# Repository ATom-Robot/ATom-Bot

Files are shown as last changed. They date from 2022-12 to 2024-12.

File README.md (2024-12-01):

# ATom-Bot 机器人
*喜欢这个项目吗？请考虑给 Star ⭐️ 以帮助改进！*

> A small desktop robot	—小型桌面交互机器人
>
> 本项目是一个桌面级小机器人，外观设计的灵感来源是Anki公司的Cozmo机器人，具备3个自由度（手臂2个、头部一个），使用自己修改的特制舵机支持关节角度回传。通过ESP32的语音唤醒+识别可以实现一些人机交互。
>
> 本项目提供了配套的全套开发资料和对应SDK以供二次开发，SDK使用说明见后文。

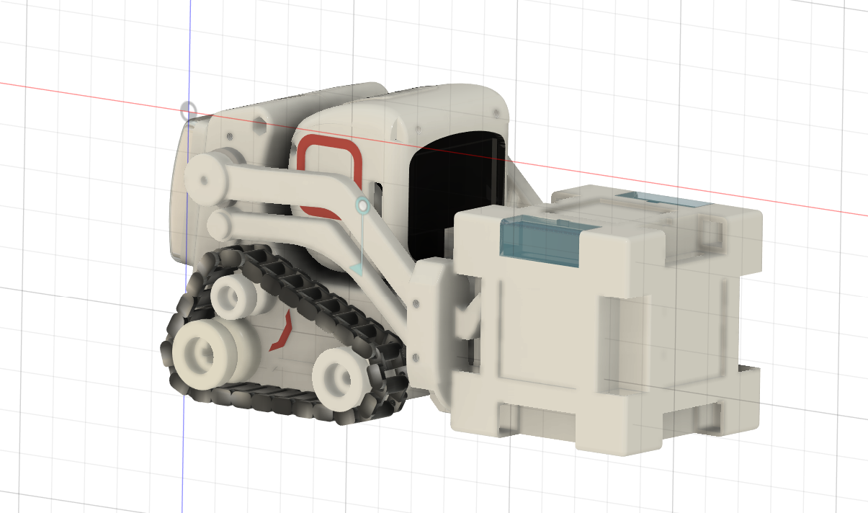
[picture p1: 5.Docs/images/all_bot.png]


机器人主要由头部+底盘两个部分组成

* 头部使用 ESP32-S3 主控担任“大脑”进行UI交互、网络通讯、轻量化AI处理；

* 底盘采用 STM32F103 主控担任“小脑”进行运动控制；

## ATom-Bot-Head 物料说明

[物料说明](https://docs.qq.com/doc/DY0lzSENnbE1SdGRn)

## ATom-Bot-Head 说明

[头部固件使用指南](https://docs.qq.com/doc/DY05KSXNtQ2pnWlF3)

## ATom-Bot-Chassis 说明

[底盘固件使用指南](https://docs.qq.com/doc/DY0NOTWp4Wk1rdlRy)

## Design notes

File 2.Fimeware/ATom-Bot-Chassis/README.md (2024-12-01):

## ATom-Bot-Chassis 说明

[底盘固件使用指南](https://docs.qq.com/doc/DY0NOTWp4Wk1rdlRy)

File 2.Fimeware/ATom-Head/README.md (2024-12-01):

# ATom-Bot-Head Fimeware

[头部固件使用指南](https://docs.qq.com/doc/DY05KSXNtQ2pnWlF3)

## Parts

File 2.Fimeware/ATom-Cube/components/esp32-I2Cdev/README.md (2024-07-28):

# I2Cdev lib for ESP32 (for MPU6050, BMP280)
I2Cdev bus implementation based on JROWBERG implementation. Modified to be more inititalized as an object, improved code consistency, some functional and structural fixes. You can find the original code here: https://github.com/jrowberg/i2cdevlib/

It is prepared to be runned as component with dependency on I2Cdev lib (https://github.com/PiotrTopa/esp32-I2Cdev). It is compatibile with PlatformIO esp-idf framework.

# Add components to your project
You need to add this repository along with I2Cdev to your project as ESP-IDF component.
```bash
cd ~/myProjects/myProject
cd components
git clone https://github.com/PiotrTopa/esp32-I2Cdev I2Cdev
```

# Example
Please see code examples at BMP280 / MPU6050 components. You can find them here:
- https://github.com/PiotrTopa/esp32-BMP280
- https://github.com/PiotrTopa/esp32-MPU6050

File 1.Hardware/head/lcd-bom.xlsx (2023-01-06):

No. | Quantity | Comment | Designator | Footprint | Value | Manufacturer Part | Manufacturer | Supplier Part | Supplier
1 | 1 | FPC-SMD_0.5-12P(翻盖下接) | CN1 | FPC-SMD_0.5S-CX-12PWB |  | FPC-SMD_0.5-12P(翻盖下接) |  | C9900007755 | LCSC
2 | 1 |  | U3 | 焊接式_TFT_1.14_135X240_13PIN
3 | 3 |  | U5,U11,U12 | 铜柱M2

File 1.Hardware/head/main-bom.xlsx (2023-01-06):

No. | Quantity | Comment | Designator | Footprint | Value | Manufacturer Part | Manufacturer | Supplier Part | Supplier
1 | 2 | TSA343G00D-250J2 | BOOT,RST | SW-SMD_L4.0-W2.9-P4.15-EH |  | TSA343G00D-250J2 | BRIGHT(博瑞泰) | C354947 | LCSC
2 | 9 | 0.1uF | C1,C4,C5,C9,C11,C14,C15,C25,C29 | C0402 | 0.1uF | 0402BB104K160NGT | Knowles(楼氏) | C2173076 | LCSC
3 | 5 | 10uF | C2,C3,C6,C24,C27 | C0402 | 10uF | CL05B104KO5NNNC | SAMSUNG(三星) | C1525 | LCSC
4 | 1 | 100nF | C7 | C0402 | 100nF | C0402X104K025T | IHHEC(禾伸堂) | C559125 | LCSC
5 | 2 | 100nF | C8,C10 | C0402 | 100nF | CL05B104KO5NNNC | SAMSUNG(三星) | C1525 | LCSC
6 | 1 | 10uF | C12 | C0402 | 10uF | C0402X104K025T | IHHEC(禾伸堂) | C559125 | LCSC
7 | 1 | 10nF | C13 | C0402 | 10nF | C0402X104K025T | IHHEC(禾伸堂) | C559125 | LCSC
8 | 1 | 10uF | C28 | C0402 | 10uF | CL05A106MQ5NUNC | SAMSUNG(三星) | C15525 | LCSC
9 | 1 | 100nF | C30 | C0402 | 100nF
10 | 1 | 10uf | C31 | C0402 | 10uf
11 | 1 | FPC-SMD_0.5-12P(翻盖下接) | CN1 | FPC-SMD_0.5S-CX-12PWB |  | FPC-SMD_0.5-12P(翻盖下接) |  | C9900007755 | LCSC
12 | 1 | SS34 | D1 | SMA_L4.3-W2.6-LS5.2-RD |  | SS34 | TDD(台冠电子) | C3032484 | LCSC
13 | 1 |  | Q1 | SOT-23_L2.9-W1.3-P1.90-LS2.4-BR |  |  |  | C444723
14 | 1 | UMH3N | Q4 | SC-70-6_L2.2-W1.3-P0.65-LS2.1-BR |  | UMH3N | CJ（江苏长电/长晶） | C62892 | LCSC
15 | 3 | 33 | R3,R7,R39 | R0402 | 33 | 0402WGF330JTCE | UNI-ROYAL(厚声) | C25105 | LCSC
16 | 3 | 4.7K | R4,R12,R46 | R0402 | 4.7K
17 | 1 | 10K | R5 | R0402
18 | 5 | 10k | R6,R8,R9,R38,R41 | R0402 | 10k | SCR0402J10K | VO(翔胜) | C3017497 | LCSC
19 | 1 | PRF15BB102RB6RC | R13 | R0402 | 1k | PRF15BB102RB6RC | muRata(村田) | C914168 | LCSC
20 | 1 | 100k | R14 | R0402 | 100k | SCR0402F100K | VO(翔胜) | C3015887 | LCSC
21 | 1 | 10R | R45 | R0402 | 10R
22 | 1 | Buttom | U2 | CONN-SMD_SH1.0A-4P-WT |  | SH1.0A-4P 卧贴 | null | C9900000720 | LCSC
23 | 3 |  | U4,U5,U11 | 铜柱M2
24 | 1 | ESP32-S3-WROOM-1(N8R8) | U6 | WIRELM-SMD_ESP32-S3-WROOM-1 |  | ESP32-S3-WROOM-1(N8R8) | ESPRESSIF 乐鑫 | C2913201 | LCSC
25 | 1 | ME6211C28M5G-N | U7 | SOT-23-5_L3.0-W1.7-P0.95-LS2.8-BR |  | ME6211C28M5G-N | MICRONE(南京微盟) | C53099 | LCSC
26 | 1 | ME6211C15M5G-N | U8 | SOT-23-5_L3.0-W1.7-P0.95-LS2.8-BR |  | ME6211C15M5G-N | MICRONE(南京微盟) | C53100 | LCSC
27 | 1 | PPFPC24/0.5mmSMD下面接触 | U9 | FPC-SMD_F0501-T-24-20T-R |  | PPFPC24/0.5mmSMD下面接触 |  | C9900014600 | LCSC
28 | 1 | MSM261S4030H0R | U10 | LGA-8_L4.0-W3.0-P1.00-BL |  | MSM261S4030H0R |  | C2840615 | LCSC
29 | 1 | PWM | U12 | CONN-SMD_SH1.0X3_W |  | SH1.0X3立贴 | null | C9900002344
30 | 1 | CH340C | U13 | SOP-16_L10.0-W3.9-P1.27-LS6.0-BL |  | CH340C | WCH(南京沁恒) | C84681 | LCSC
31 | 1 | LP2992IM5-3.3 | U16 | SOT-23-5_L2.9-W1.6-P0.95-LS2.8-BL |  | LP2992IM5-3.3 | National Semiconductor | C3751592 | LCSC
32 | 1 | NS4168 | U17 | ESOP-8_L4.9-W3.9-P1.27-LS6.0-BL-EP2.0 |  | NS4168 | Shenzhen Nsiway Tech
33 | 1 | TYPEC-304-BCP16 | USB | USB-C-SMD_TYPEC-304-BCP16 |  | TYPEC-304-BCP16 | XUNPU(讯普) | C720629 | LCSC
34 | 1 |  | VCC | LED0402-RD_GREEN |  |  |  | C71911

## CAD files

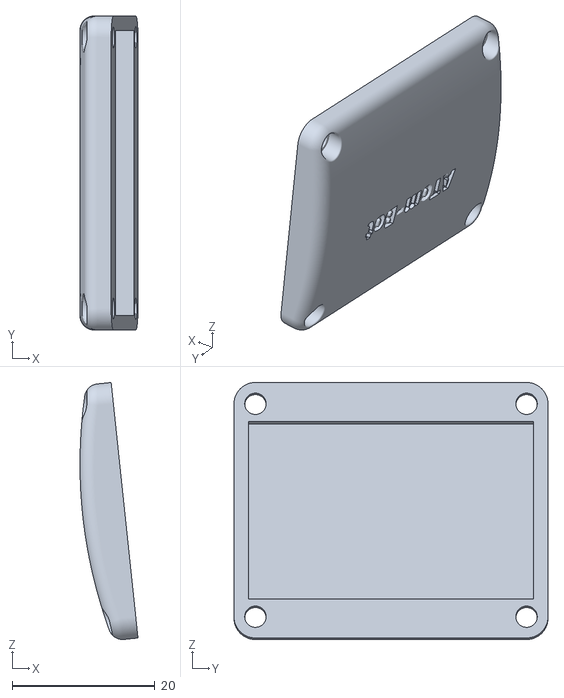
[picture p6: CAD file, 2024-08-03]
4.3D_Model/Body/电池背仓.stl
8.13 x 44.0 x 36.0

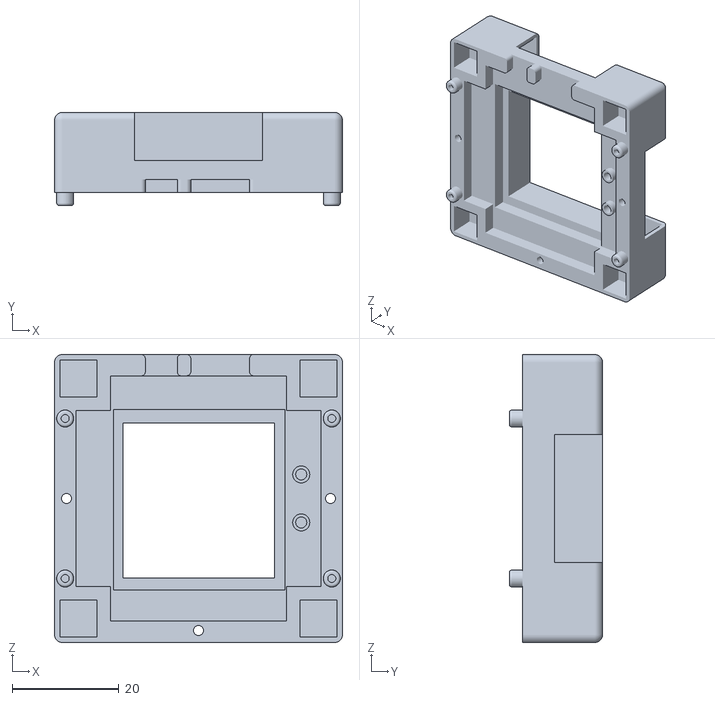
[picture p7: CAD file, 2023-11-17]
4.3D_Model/Cube/魔方顶部.stl
54.0 x 17.5 x 54.0

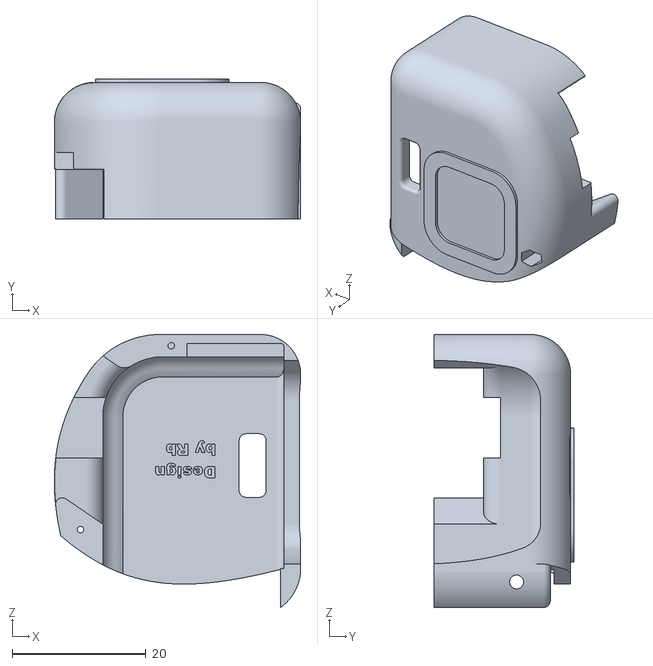
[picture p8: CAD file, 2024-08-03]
4.3D_Model/Body/身体-头部--左.stl
36.8 x 20.9 x 40.8

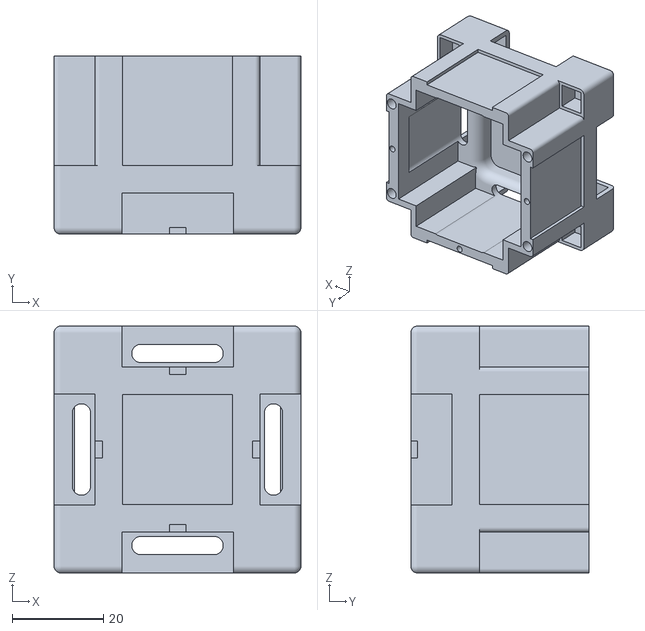
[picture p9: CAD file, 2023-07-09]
4.3D_Model/Cube/魔方主体.stl
54.0 x 39.0 x 54.0

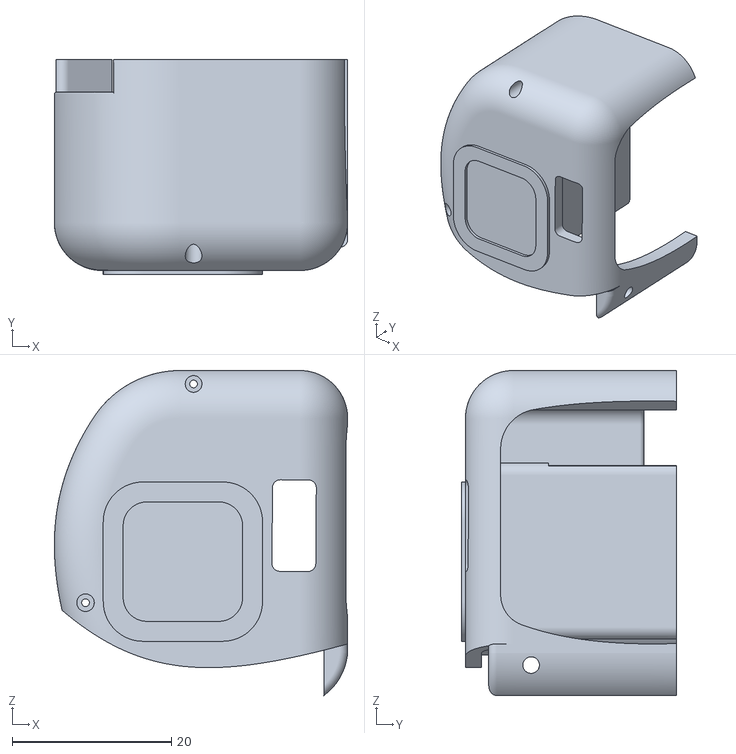
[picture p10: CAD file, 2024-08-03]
4.3D_Model/Body/身体-头部--右.stl
36.8 x 27.0 x 40.8

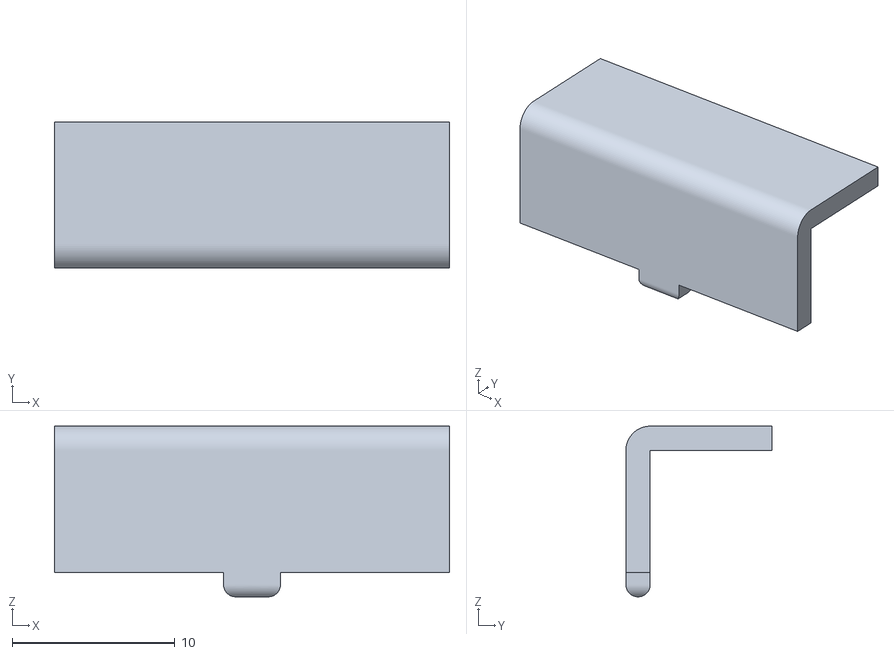
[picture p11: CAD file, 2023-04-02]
4.3D_Model/Cube/透明罩x4.stl
24.3 x 9.00 x 10.5

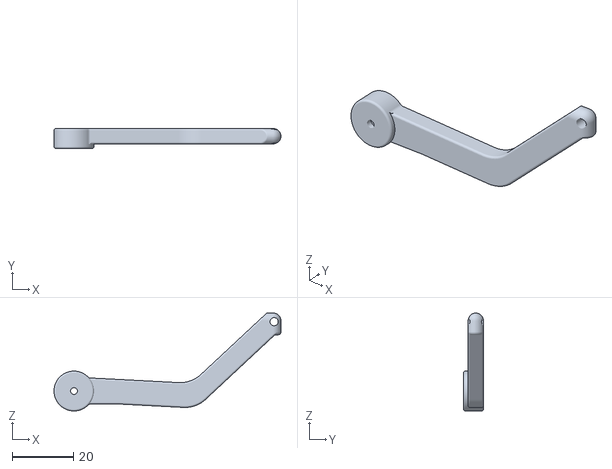
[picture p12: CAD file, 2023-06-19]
4.3D_Model/Body/alram-l-tx2.stl
74.0 x 6.50 x 31.9

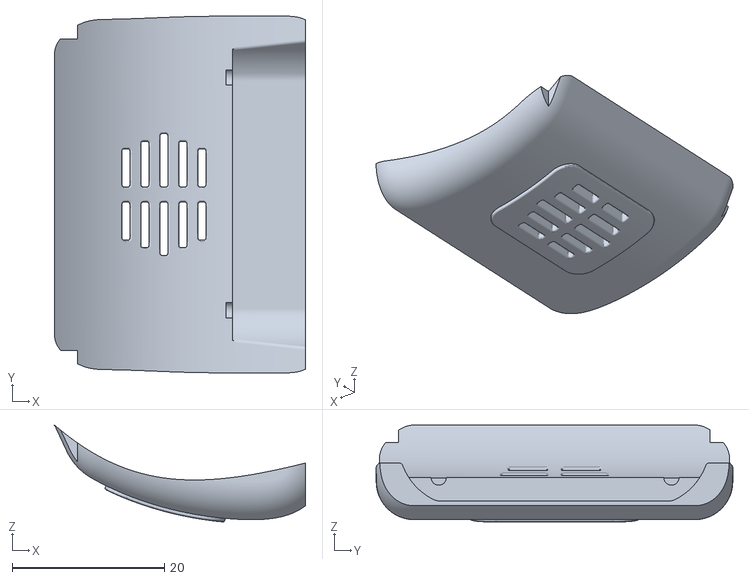
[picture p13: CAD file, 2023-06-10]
4.3D_Model/Body/头顶.stl
33.0 x 46.9 x 12.7

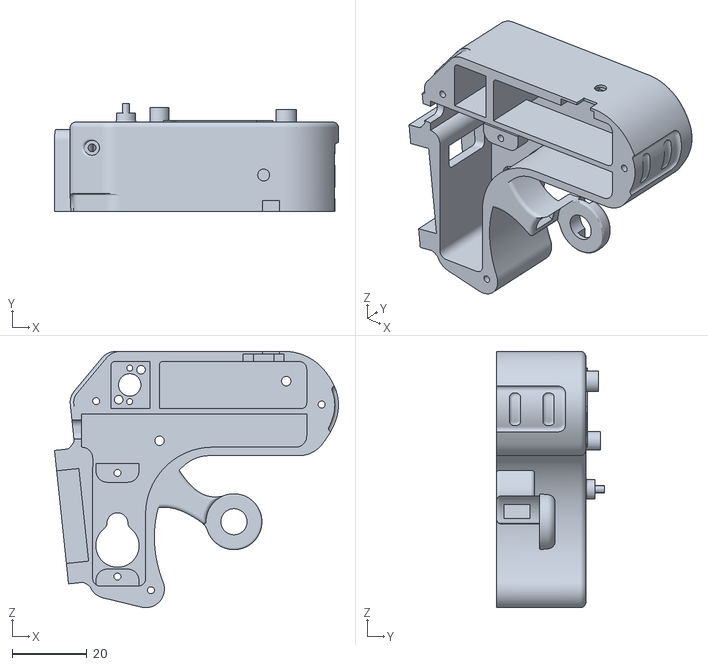
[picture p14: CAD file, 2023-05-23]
4.3D_Model/Body/身体-右-sg90.stl
76.2 x 29.0 x 68.8

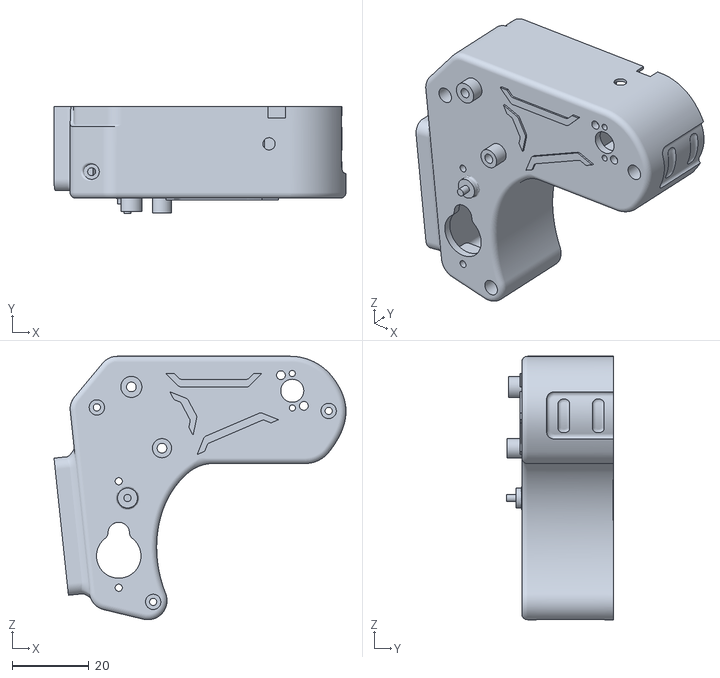
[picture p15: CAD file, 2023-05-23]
4.3D_Model/Body/身体-左-sg90.stl
76.2 x 28.0 x 68.8

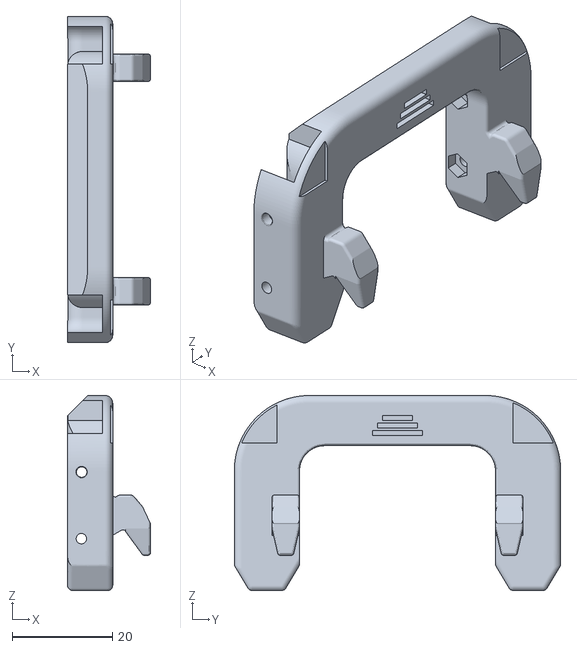
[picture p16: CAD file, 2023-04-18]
4.3D_Model/Body/钩子.stl
16.5 x 65.0 x 38.8

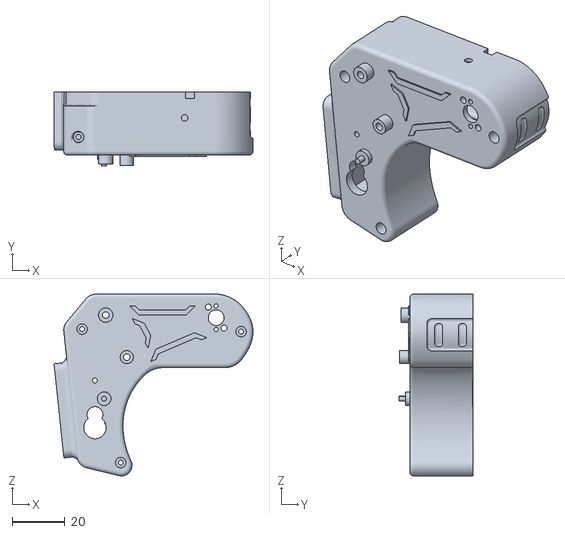
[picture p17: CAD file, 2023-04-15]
4.3D_Model/Body/身体-左-4.3g舵机.stl
75.7 x 28.0 x 69.2

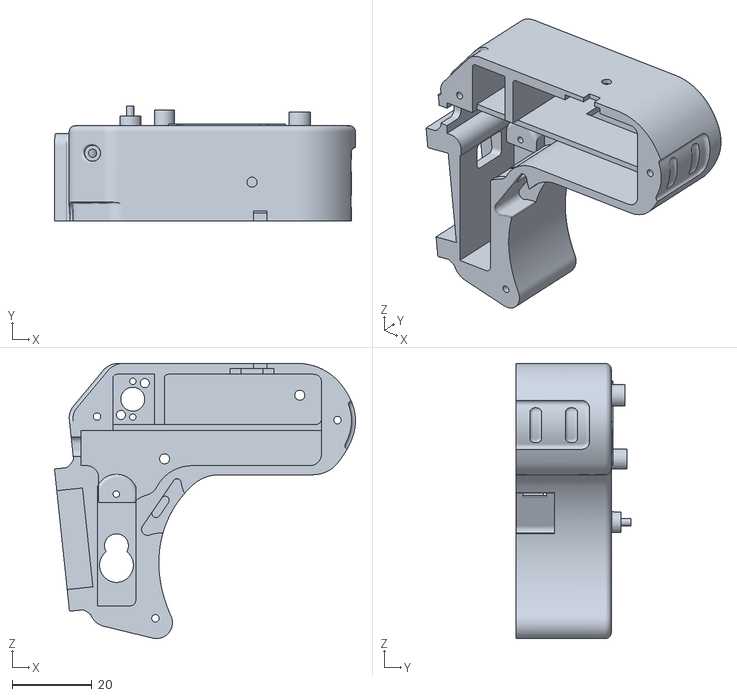
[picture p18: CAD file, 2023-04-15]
4.3D_Model/Body/身体-右-4.3g舵机.stl
75.7 x 29.0 x 69.2

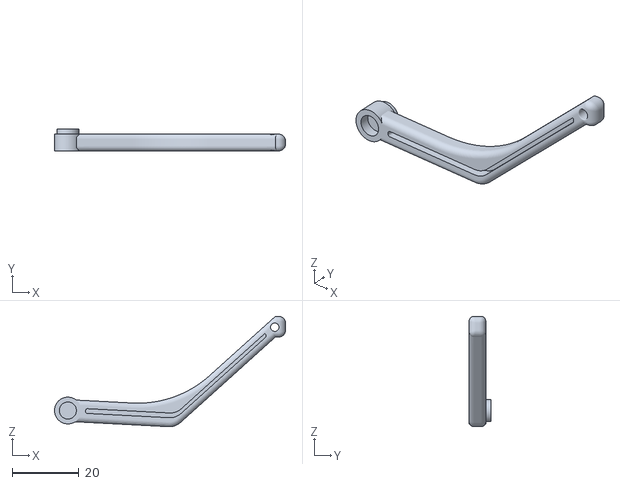
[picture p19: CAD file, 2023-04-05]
4.3D_Model/Body/alram-r-dx2.stl
69.0 x 6.50 x 33.0

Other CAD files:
2.Fimeware/ATom-Head/components/decoder_jpeg_ijg/jpeg-9a/jdosamsc.obj
2.Fimeware/ATom-Head/components/decoder_jpeg_ijg/jpeg-9a/jdosabcc.obj
4.3D_Model/Body/alram-r-tx2.stl
4.3D_Model/Body/alram-l-dx2.stl
4.3D_Model/Body/whell-smallx2.stl
4.3D_Model/Body/whell1-bigx2.stl
4.3D_Model/Body/whell2-bigx2.stl
4.3D_Model/Body/轮毂固定栓x2.stl

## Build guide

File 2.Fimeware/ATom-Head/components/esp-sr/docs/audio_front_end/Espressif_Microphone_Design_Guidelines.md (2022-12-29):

# Espressif Microphone Design Guidelines
> This document provides microphone design guidelines and suggestions for the ESP32-S3 series of audio development boards.

###Electrical Performance
1. Type: omnidirectional MEMS microphone
2. Sensitivity
	- Under 1 Pa sound pressure, it should be no less than -38 dBV for analog microphones, and -26 dB for digital microphones. 
	- The tolerance should be controlled within ±2 dB, and within ±1 dB for microphone arrays.
3. Signal-to-noise ratio (SNR)
	- No less than 62 dB. Higher than 64 dB is recommended.
	- Frequency response fluctuates within ±3 dB from 50 to 16 kHz. 
	- PSRR should be larger than 55 dB for MEMS microphones.
		
---
###Structure Design
1. The aperture or width of the microphone hole is recommended to be greater than 1 mm, the pickup pipe should be as short as possible, and the cavity should be as small as possible to ensure that the resonance frequency of the microphone and structural components is above 9 kHz.
2. The depth and diameter of the pickup hole are less than 4:1, and the thickness of the shell is recommended to be 1 mm. If the shell is too thick, the opening area must be increased.
3. The microphone hole must be protected by an anti-dust mesh.
4. Silicone sleeve or foam must be added between the microphone and the device shell for sealing and shockproofing, and an interference fit design is required to ensure the tightness of the microphone.
5. The microphone hole cannot be blocked. The bottom microphone hole needs to be increased in structure to prevent it from being blocked by the desktop.
6. The microphone should be placed far away from the speaker and other objects that can produce noise or vibration, and be isolated and buffered by rubber pads from the speaker sound cavity.

---
###Microphone Array Design
1. Type: omnidirectional MEMS microphone. Use the same models from the same manufacturer for the array. Not recommended mixing different microphones.
2. The sensitivity difference among microphones in the array is within 3 dB.
3. The phase difference among the microphones in the array is controlled within 10°.
4. It is recommended to keep the structural design of each microphone in the array the same to ensure consistency.
5. Two-microphone solution: the distance between the microphones should be 4 ~ 6.5 cm, the axis connecting them should be parallel to the horizontal line, and the center of the two microphones should be horizontally as close as possible to the center of the product.
6. Three-microphone solution: the microphones are equally spaced and distributed in a perfect circle with the angle 120 degrees from each other, and the spacing should be 4 ~ 6.5 cm.

---
###Microphone Structure Tightness
Use plasticine or other materials to seal the microphone pickup hole and compare how much the signals collected by the microphone decrease by before and after the seal. 25 dB is qualified, and 30 dB is recommended. Below are the test procedures.

1. Play white noise at 0.5 meters above the microphone, and keep the volume at the microphone 90 dB. 
2. Use the microphone array to record for more than 10 s, and store it as recording file A.
3. Use plasticine or other materials to block the microphone pickup hole, record for more than 10 s, and store it as recording file B.
4. Compare the frequency spectrum of the two files and make sure that the overall attenuation in the 100 ~ 8 kHz frequency band is more than 25 dB.

---
###Echo Reference Signal Design
1. It is recommended that the echo reference signal be as close to the speaker side as possible, and recover from the DAC post-stage and PA pre-stage.
2. When the speaker volume is at its maximum, the echo reference signal input to the microphone should not have saturation distortion. At the maximum volume, the speaker amplifier output THD is less than 10% at 100 Hz, less than 6% at 200 Hz, and less than 3% above 350 Hz.
3. When the speaker volume is at its maximum, the sound pressure picked up by the microphone does not exceed 102 dB @ 1 kHz.
4. The echo reference signal voltage does not exceed the maximum allowed input voltage of the ADC. If it is too high, an attenuation circuit should be added.
5. A low-pass filter should be added to introduce the reference echo signal from the output of the Class D power amplifier. The cutoff frequency of the filter is recommended to be more than 22 kHz.
6. When the volume is played at the maximum, the recovery signal peak value is -3 to -5 dB.   

---                                                                                                                                          
###Microphone Array Consistency
It is required that the difference between the sampled signals of each microphone is less than 3 dB. Below are the test procedures.

1. Play white noise at 0.5 meters above the microphone, and keep the volume at the microphone 90 dB.
2. Use the microphone array to record for more than 10 s, and check whether the recording amplitude and audio sampling rate of each microphone are consistent.

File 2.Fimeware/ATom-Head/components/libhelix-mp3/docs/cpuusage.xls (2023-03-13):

Fixed-point MP3 average CPU usage | Sample Rate | Bit Rate | Channels | Processor Model
/datatype/mp3/codec/fixpt - 08/05/03 |  |  |  | ARM7TDMI | ARM9TDMI-REV2 | ARM920T | ARM9E | StrongARM1 | XScale
 | 48000 | 320 kbps | 2 | 30 MHz | 24 MHz | 27 MHz | 20 MHz | 20 MHz | 20 MHz
Notes: | 44100 | 128 kbps | 2 | 26 MHz | 21 MHz | 24 MHz | 17 MHz | 17 MHz | 17 MHz
* Numbers are from ARMulator, simulated
zero-wait state memory
* Compiled using ARM ADS 1.2 with
appropriate target CPU

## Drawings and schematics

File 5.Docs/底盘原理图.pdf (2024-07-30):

## GND

## USB_5V

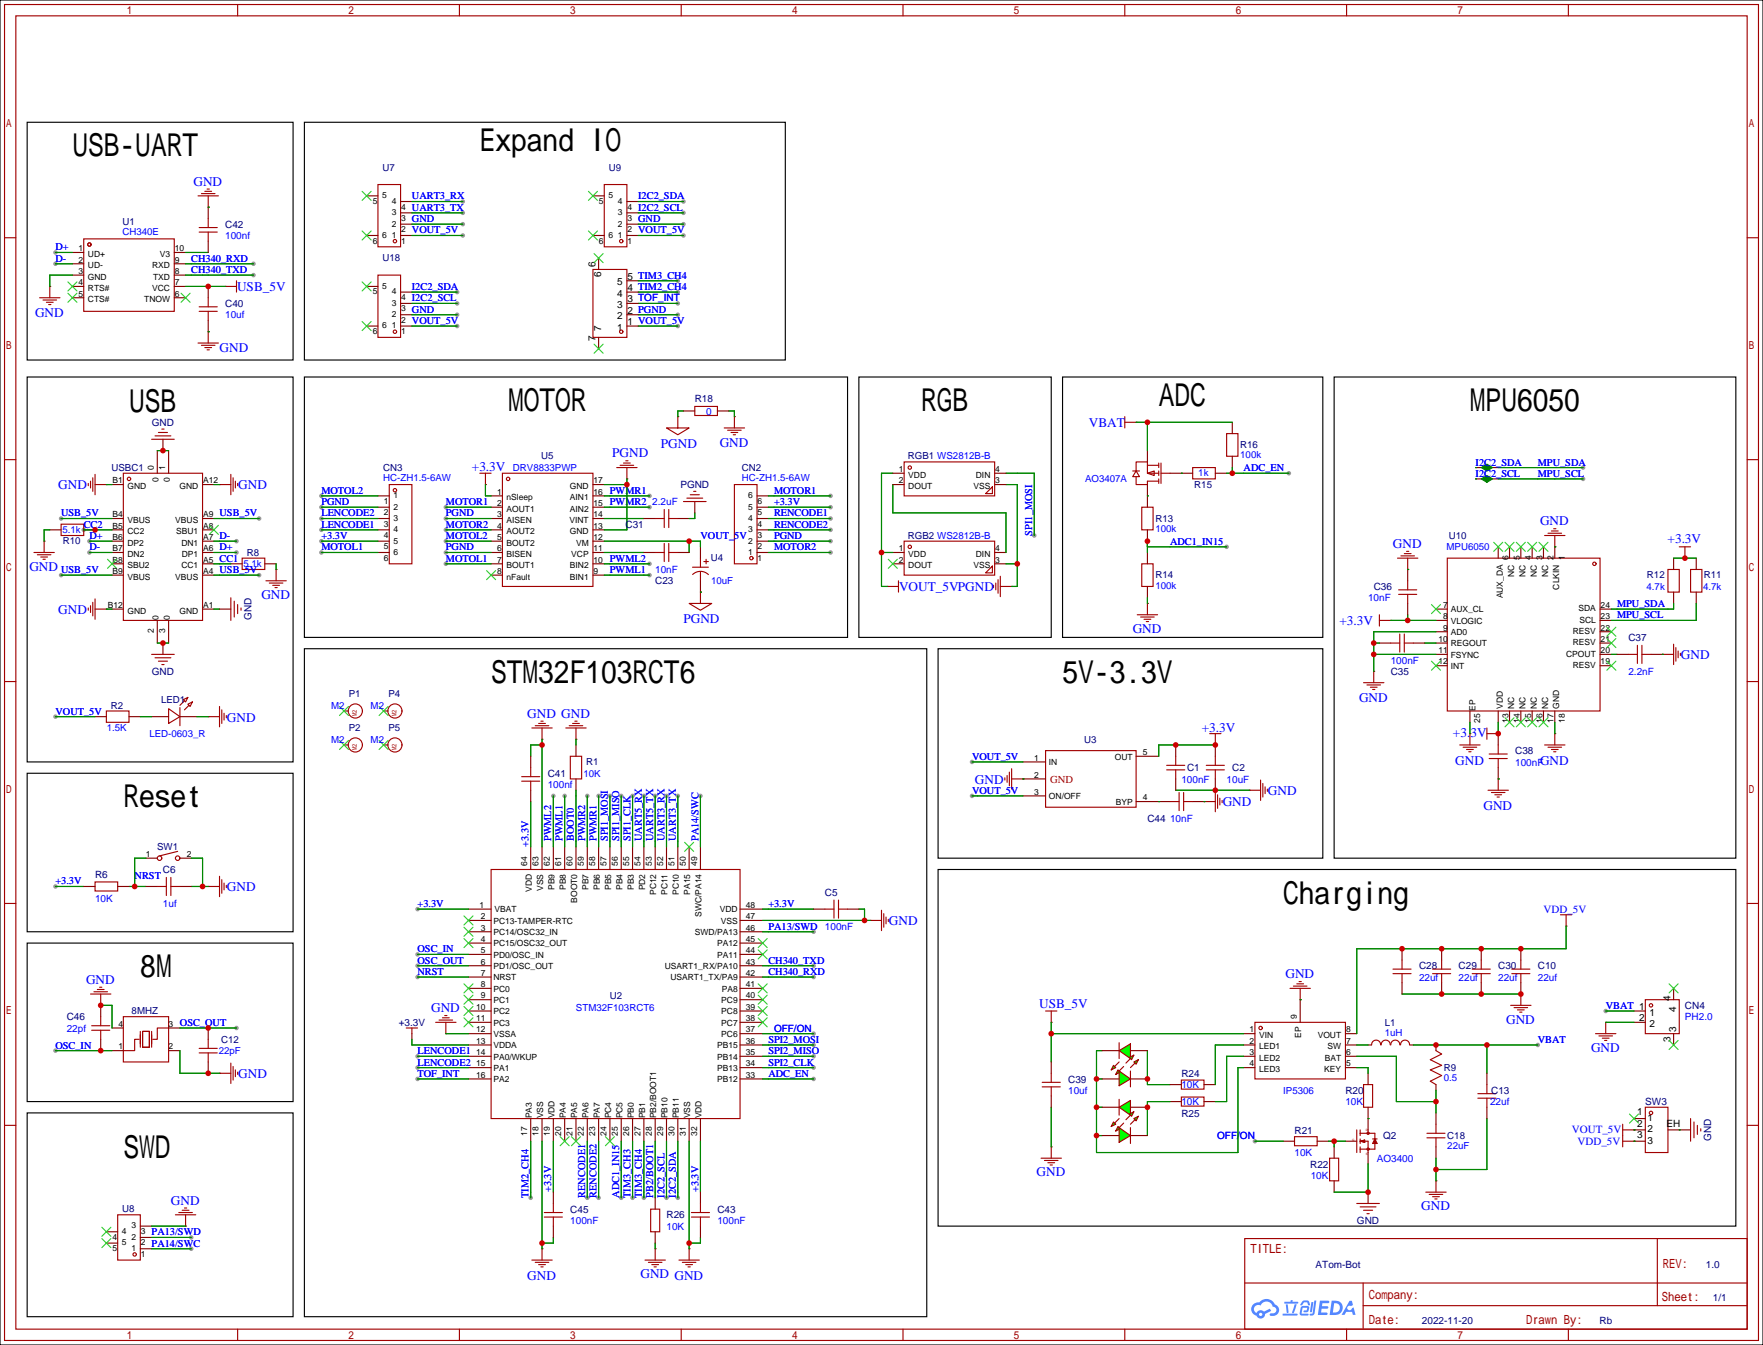
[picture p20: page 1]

BIN2 10 VCP 11 VM 12 GND 13 VINT 14 AIN2 15 AIN1 16 GND 17

VDD 13 NC 14 NC 15 NC 16 NC 17 GND 18

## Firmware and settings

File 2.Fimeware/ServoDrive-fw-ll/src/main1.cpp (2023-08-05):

#include <cstring>
#include "common_inc.h"
#include "configurations.h"

Motor motor;
BoardConfig_t boardConfig;


/* Default Entry -------------------------------------------------------*/
void Main()
{
    // Read data from Flash
    EEPROM eeprom;
    eeprom.get(0, boardConfig);
    if (boardConfig.configStatus != CONFIG_OK) // use default settings
    {
        boardConfig = BoardConfig_t
        {
            .configStatus = CONFIG_OK,
            .nodeId = 4, // 7bit address, has to be even number
            .initPos = 90,
            .toqueLimit =  0.95,
            .velocityLimit = 0,
            .adcValAtAngleMin = 250,
            .adcValAtAngleMax = 3000,
            .mechanicalAngleMin = 0,
            .mechanicalAngleMax = 180,
            .dceKp = 10,
            .dceKv = 0,
            .dceKi = 0,
            .dceKd = 50,
            .enableMotorOnBoot = false
        };
        eeprom.put(0, boardConfig);
    }
    motor.SetTorqueLimit(boardConfig.toqueLimit);
    motor.mechanicalAngleMin = boardConfig.mechanicalAngleMin;
    motor.mechanicalAngleMax = boardConfig.mechanicalAngleMax;
    motor.adcValAtAngleMin = boardConfig.adcValAtAngleMin;
    motor.adcValAtAngleMax = boardConfig.adcValAtAngleMax;
    motor.dce.kp = boardConfig.dceKp;
    motor.dce.ki = boardConfig.dceKi;
    motor.dce.kv = boardConfig.dceKv;
    motor.dce.kd = boardConfig.dceKd;
    motor.dce.setPointPos = boardConfig.initPos;
    motor.SetEnable(boardConfig.enableMotorOnBoot);
    // Init PWM
    LL_TIM_EnableCounter(TIM3);
    LL_TIM_CC_EnableChannel(TIM3, LL_TIM_CHANNEL_CH1);
    LL_TIM_CC_EnableChannel(TIM3, LL_TIM_CHANNEL_CH2);
    LL_TIM_OC_SetCompareCH1(TIM3, 0);
    LL_TIM_OC_SetCompareCH2(TIM3, 0);

    // Start receive data
    MY_I2C1_Init(boardConfig.nodeId);
    LL_mDelay(10);
    // Start control loop at 200Hz
    LL_TIM_EnableIT_UPDATE(TIM14);
    LL_TIM_EnableCounter(TIM14);


    while (1)
    {
        if (boardConfig.configStatus == CONFIG_COMMIT)
        {
            boardConfig.configStatus = CONFIG_OK;
            eeprom.put(0, boardConfig);
        }
        else if (boardConfig.configStatus == CONFIG_RESTORE)
        {
            eeprom.put(0, boardConfig);
            HAL_NVIC_SystemReset();
        }
        /* for debug */
        //LL_GPIO_TogglePin(GPIOA,GPIO_PIN_1);
    }
}


/* Callbacks -------------------------------------------------------*/
// void HAL_ADC_ConvCpltCallback(ADC_HandleTypeDef* AdcHandle)
// {

// }


// // Command handler
void I2C_SlaveDMARxCpltCallback()
{
    ErrorStatus state;

    float valF = *((float *)(i2cDataRx + 1));

    i2cDataTx[0] = i2cDataRx[0];
    switch (i2cDataRx[0])
    {
    case 0x01:  // Set angle
    {
        motor.dce.setPointPos = valF;
        auto *b = (unsigned char *) & (motor.angle);
        for (int i = 0; i < 4; i++)
            i2cDataTx[i + 1] = *(b + i);
        break;
    }
    case 0x02: // Set velocity
    {
        motor.dce.setPointVel = valF;
        auto *b = (unsigned char *) & (motor.velocity);
        for (int i = 0; i < 4; i++)
            i2cDataTx[i + 1] = *(b + i);
        break;
    }
    case 0x03: // Set torque
    {
        motor.SetTorqueLimit(valF);
        auto *b = (unsigned char *) & (motor.angle);
        for (int i = 0; i < 4; i++)
            i2cDataTx[i + 1] = *(b + i);
        break;
    }
    case 0x11: // Get angle
    {
        auto *b = (unsigned char *) & (motor.angle);
        for (int i = 0; i < 4; i++)
            i2cDataTx[i + 1] = *(b + i);
        break;
    }
    case 0x12: // Get velocity
    {
        auto *b = (unsigned char *) & (motor.velocity);
        for (int i = 0; i < 4; i++)
            i2cDataTx[i + 1] = *(b + i);
        break;
    }
    case 0x21: // Set id
    {
        boardConfig.nodeId = i2cDataRx[1];
        boardConfig.configStatus = CONFIG_COMMIT;
        auto *b = (unsigned char *) & (motor.angle);
        for (int i = 0; i < 4; i++)
            i2cDataTx[i + 1] = *(b + i);
        break;
    }
    case 0x22: // Set kp
    {
        motor.dce.kp = valF;
        boardConfig.dceKp = valF;
        boardConfig.configStatus = CONFIG_COMMIT;
        auto *b = (unsigned char *) & (motor.angle);
        for (int i = 0; i < 4; i++)
            i2cDataTx[i + 1] = *(b + i);
        break;
    }
    case 0x23: // Set ki
    {
        motor.dce.ki = valF;
        boardConfig.dceKi = valF;
        boardConfig.configStatus = CONFIG_COMMIT;
        auto *b = (unsigned char *) & (motor.angle);
        for (int i = 0; i < 4; i++)
            i2cDataTx[i + 1] = *(b + i);
        break;
    }
    case 0x24: // Set kv
    {
        motor.dce.kv = valF;
        boardConfig.dceKv = valF;
        boardConfig.configStatus = CONFIG_COMMIT;
        auto *b = (unsigned char *) & (motor.angle);
        for (int i = 0; i < 4; i++)
            i2cDataTx[i + 1] = *(b + i);
        break;
    }
    case 0x25: // Set kd
    {
        motor.dce.kd = valF;
        boardConfig.dceKd = valF;
        boardConfig.configStatus = CONFIG_COMMIT;
        auto *b = (unsigned char *) & (motor.angle);
        for (int i = 0; i < 4; i++)
            i2cDataTx[i + 1] = *(b + i);
        break;
    }
    case 0x26: // Set torque limit
    {
        motor.SetTorqueLimit(valF);
        boardConfig.toqueLimit = valF;
        boardConfig.configStatus = CONFIG_COMMIT;
        auto *b = (unsigned char *) & (motor.angle);
        for (int i = 0; i < 4; i++)
            i2cDataTx[i + 1] = *(b + i);
        break;
    }
    case 0x27: // Set init pos
    {
        boardConfig.initPos = valF;
        boardConfig.configStatus = CONFIG_COMMIT;
        auto *b = (unsigned char *) & (motor.angle);
        for (int i = 0; i < 4; i++)
            i2cDataTx[i + 1] = *(b + i);
        break;
    }
    case 0xff:
        motor.SetEnable(i2cDataRx[1] != 0);
        break;
    default:
        break;
    }
    do
    {
        state = Slave_Transmit(i2cDataTx, 5, 5000);
    }
    while (state != SUCCESS);
    if (i2cDataRx[0] == 0x21)
    {
        Set_ID(boardConfig.nodeId);
    }

}


// Control loop
void TIM14_PeriodElapsedCallback()
{
    // Read sensor data
    LL_DMA_EnableChannel(DMA1, LL_DMA_CHANNEL_1);
    LL_ADC_REG_StartConversion(ADC1);

    motor.angle = motor.mechanicalAngleMin +
                  (motor.mechanicalAngleMax - motor.mechanicalAngleMin) *
                  ((float) adcData[0] - (float) motor.adcValAtAngleMin) /
                  ((float) motor.adcValAtAngleMax - (float) motor.adcValAtAngleMin);
    // Calculate PID
    motor.CalcDceOutput(motor.angle, 0);
    motor.SetPwm((int16_t) motor.dce.output);
}

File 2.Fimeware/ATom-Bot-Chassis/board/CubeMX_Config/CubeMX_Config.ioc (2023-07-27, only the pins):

Mcu.UserName=STM32F103RCTx
PA0-WKUP.Signal=S_TIM2_CH1_ETR
PA1.Signal=S_TIM2_CH2
PA10.Signal=USART1_RX
PA13.Signal=SYS_JTMS-SWDIO
PA14.Signal=SYS_JTCK-SWCLK
PA6.Signal=S_TIM3_CH1
PA7.Signal=S_TIM3_CH2
PA9.Signal=USART1_TX
PB10.Signal=I2C2_SCL
PB11.Signal=I2C2_SDA
PB3.Signal=SPI1_SCK
PB5.Signal=SPI1_MOSI
PB6.Signal=S_TIM4_CH1
PB7.Signal=S_TIM4_CH2
PB8.Signal=S_TIM4_CH3
PB9.Signal=S_TIM4_CH4
PC10.Signal=USART3_TX
PC11.Signal=USART3_RX
PC5.Signal=ADCx_IN15
PD0-OSC_IN.Signal=RCC_OSC_IN
PD1-OSC_OUT.Signal=RCC_OSC_OUT

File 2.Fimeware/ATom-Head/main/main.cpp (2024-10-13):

#include "esp_err.h"
#include "esp_log.h"
#include "bsp_storage.h"

#include "app_lcd.h"
#include "app_wifi.h"
#include "app_camera.h"
#include "app_speech.h"
#include "app_speaker.h"
#include "app_apriltag.h"
#include "app_player.h"
#include "app_shell.h"
#include "app_rtsp.h"
#include "app_joint.h"
#include "app_uart.h"
#include "app_tcpserver.h"
#include "stream_server.h"

extern "C" void app_main()
{
    QueueHandle_t xQueueLCDFrame = xQueueCreate(2, sizeof(camera_fb_t *));

    audio_player_config_t config =
    {
        .mute_fn = NULL,
        .clk_set_fn = bsp_codec_set_fn,
        .write_fn = bsp_i2s_write,
        .priority = configMAX_PRIORITIES - 5,
        .base_path = "/spiffs/mp3"
    };

    ESP_ERROR_CHECK(bsp_spiffs_init("model", "/srmodel", 4));
    ESP_ERROR_CHECK(bsp_spiffs_init("storage", "/spiffs", 4));

    ESP_ERROR_CHECK(App_Camera_Init(PIXFORMAT_JPEG, FRAMESIZE_QVGA, 3, xQueueLCDFrame));
    ESP_ERROR_CHECK(App_Lcd_Init(xQueueLCDFrame, NULL, true));
    ESP_ERROR_CHECK(App_Speech_Init());
    ESP_ERROR_CHECK(App_Speaker_Init());
    ESP_ERROR_CHECK(App_Joint_Init());

    ESP_ERROR_CHECK(App_Speech_run());
    ESP_ERROR_CHECK(App_Camera_run());
    ESP_ERROR_CHECK(App_Lvgl_run());
    ESP_ERROR_CHECK(App_Wifi_run());
    ESP_ERROR_CHECK(APP_TcpServer_run());
    ESP_ERROR_CHECK(APP_Player_run(config));

    ESP_ERROR_CHECK(App_Stream_run(xQueueLCDFrame, true));
    ESP_ERROR_CHECK(App_Shell_run());
    ESP_ERROR_CHECK(APP_Uart_run());
}

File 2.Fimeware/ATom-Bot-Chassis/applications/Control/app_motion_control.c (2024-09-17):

/*
 * SPDX-License-Identifier: Apache-2.0
 *
 * Change Logs:
 * Date           Author       Notes
 * 2023-06-11     Rbb666       the first version
 * 2023-07-29     Rbb666       add angel pid
 */
#include <rtthread.h>
#include <rtdevice.h>
#include <board.h>

#include "AT_Math.h"
#include "bsp_pid.h"
#include "bsp_motor.h"
#include "bsp_encoder.h"
#include "dmp_port_rtt.h"
#include "ano.h"

#define DBG_SECTION_NAME  "app-control"
#define DBG_LEVEL         DBG_LOG
#include <rtdbg.h>

#define HWTIMER_DEV_NAME   "timer4"

typedef struct
{
    int32_t Target_Velocity;
    int32_t Reality_Velocity;

    int32_t Target_Position;
    int32_t Reality_Position;
} velocity_dt;

static velocity_dt wheel_dt[2];
static int32_t motor_pwm[2];
static _PID_val_st yaw_val;
uint8_t use_pid_ctrl = 1;

static void Motion_Set_PWM(int motor_Left, int motor_Right)
{
    Motor_Set_Pwm(MOTOR_ID_1, motor_Left);
    Motor_Set_Pwm(MOTOR_ID_2, motor_Right);
}

int leftSpeedNow = 0;

static rt_err_t timeout_cb(rt_device_t dev, rt_size_t size)
{
    wheel_dt[LEFT].Reality_Velocity = -Encoder_Get_Counter(ENCODER_ID_A);
    wheel_dt[RIGHT].Reality_Velocity = Encoder_Get_Counter(ENCODER_ID_B);

    wheel_dt[LEFT].Reality_Position += wheel_dt[LEFT].Reality_Velocity;
    wheel_dt[RIGHT].Reality_Position += wheel_dt[RIGHT].Reality_Velocity;
#if 0
    float left_speed1, left_speed2;
    left_speed1 = Motor_Speed(wheel_dt[LEFT].Reality_Velocity, 7, 100, 10);
#endif
    if (use_pid_ctrl)
    {
        for (uint8_t i = 0; i < 2; i++)
        {
            Position_PID(&pid_pos[i], wheel_dt[i].Target_Position, wheel_dt[i].Reality_Position);

            motor_pwm[i] = limit_amplitude(pid_pos[i].output, wheel_dt[i].Target_Velocity);
            motor_pwm[i] = Incremental_PID(&pid_vel[i], motor_pwm[i], wheel_dt[i].Reality_Velocity);
        }
#if 0
        // not use
        if (angel_control && (ABS(rec_target_yaw - (int)robot_imu_dmp_data.yaw) > 2))
        {
            /* 角度环 */
            PID_calculate(10, rec_target_yaw, robot_imu_dmp_data.yaw, &pid_yaw, &yaw_val, 20, 100);
        }
        else
        {
            angel_control = RT_FALSE;
            yaw_val.out = 0;
        }
#endif
        Motion_Set_PWM(motor_pwm[LEFT] + yaw_val.out, motor_pwm[RIGHT] - yaw_val.out);
    }

    return RT_EOK;
}

static void Motion_Control_20ms(void *parameter)
{
    while (1)
    {
        for (uint8_t i = 0; i < 2; i++)
        {
            /* 转速 0-300 */
            wheel_dt[i].Target_Velocity = Rpm_Encoder_Cnt(rec_target_rpm[i], 7, 100, 10);
            /* 位置 */
            wheel_dt[i].Target_Position = Num_Encoder_Cnt(rec_target_motor_num, 7, 100);
        }
#if USING_ANO_DEBUG
        ano_send_user_data(1, wheel_dt[LEFT].Target_Position,   \
                           wheel_dt[LEFT].Reality_Position,     \
                           wheel_dt[LEFT].Target_Velocity,      \
                           wheel_dt[LEFT].Reality_Velocity,     \
                           0,                                   \
                           0);
#endif
        rt_thread_mdelay(10);
    }
}

void app_motion_ctrl_init(void)
{
    rt_thread_t tid;

    tid = rt_thread_create("ctrl", Motion_Control_20ms, RT_NULL,
                           1024, 15, 20);
    RT_ASSERT(tid != RT_NULL);
    rt_thread_startup(tid);
}

int control_hwtimer(void)
{
    rt_err_t ret = RT_EOK;
    rt_hwtimerval_t timeout_s;
    rt_device_t hw_dev = RT_NULL;
    rt_hwtimer_mode_t mode;
    rt_uint32_t freq = 10000;

    hw_dev = rt_device_find(HWTIMER_DEV_NAME);
    if (hw_dev == RT_NULL)
    {
        rt_kprintf("hwtimer sample run failed! can't find %s device!\n", HWTIMER_DEV_NAME);
        return RT_ERROR;
    }

    ret = rt_device_open(hw_dev, RT_DEVICE_OFLAG_RDWR);
    if (ret != RT_EOK)
    {
        rt_kprintf("open %s device failed!\n", HWTIMER_DEV_NAME);
        return ret;
    }

    rt_device_set_rx_indicate(hw_dev, timeout_cb);
    rt_device_control(hw_dev, HWTIMER_CTRL_FREQ_SET, &freq);

    mode = HWTIMER_MODE_PERIOD;
    ret = rt_device_control(hw_dev, HWTIMER_CTRL_MODE_SET, &mode);
    if (ret != RT_EOK)
    {
        rt_kprintf("set mode failed! ret is :%d\n", ret);
        return ret;
    }

    timeout_s.sec = 0;
    timeout_s.usec = 10000;
    if (rt_device_write(hw_dev, 0, &timeout_s, sizeof(timeout_s)) != sizeof(timeout_s))
    {
        rt_kprintf("set timeout value failed\n");
        return RT_ERROR;
    }

    return ret;
}

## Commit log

2022-12-10 The first commit
    [kconfig-language.txt, kconfig.txt]
2022-12-13 add pulse device
2022-12-17 Add pid device
2022-12-18 Add new pid device
2022-12-19 Update pid paramter
2022-12-24 Add camera device
2022-12-25 Add camera to lvgl
2022-12-26 Add MJPEG decode support
    [jconfig.cfg, jconfig.txt, jdosabcc.obj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]
2022-12-29 Add esp-dl and esp-sr component
    [mnist_mxnet-0010.params, partitions.csv]
2022-12-30 Add speek audio device
    [partitions.csv]
2022-12-30 Modify cache size
    [partitions.csv]
2022-12-31 Add pcb 3D model
2023-01-06 Add hardware file
    [lcd-bom.xlsx, main-bom.xlsx]
2023-01-06 Add bom-html
2023-02-25 Fix mpu6050 dmp data error problem
    [bsp_kinematics.c, bsp_kinematics.h, bsp_pid.c]
2023-02-27 Update esp-camera
2023-02-28 Add cube model
    [透明盖.step, 魔方主体.step, 魔方顶部.step]
2023-03-05 Add voltage detection
2023-03-07 [Hardware]Add servo-board gerber
2023-03-08 [Fimeware]Add servo fw
    [configurations.h]
2023-03-11 [Model]Update cube model
    [魔方主体.step, 魔方顶部.step]
2023-03-12 [Model]Add body model
    [alram-l-t.stl, alram-r-t.stl, whell.stl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]
2023-03-13 [Fimeware]Add mp3 decode
    [cpuusage.xls, memory.xls, partitions.csv]
2023-03-18 [model]Add wheel
    [whell-big-2.stl, whell-big.stl, whell.stl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]
2023-03-19 [Fimeware]Add servo hal proj
    [configurations.h]
2023-03-25 [Fimeware]Add cube proj
    [partitions.csv]
2023-03-25 [Fimeware]Add cube led
2023-03-27 [Fimeware]Update esp32 partitions
    [partitions.csv]
2023-04-01 [Model]Update body and cube model
    [身体-右.stl, 身体-左.stl, 轮毂固定栓.stl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]
2023-04-02 [Model]Add some body and cube model
    [身体-右.stl, 身体-左.stl, 透明罩x4.stl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]
2023-04-03 [Fimeware]Update screen driver
2023-04-05 [Fimeware]Add webcamera support
    [alram-l-d.stl, alram-r-d.stl]
2023-04-06 [Model]Update body model
    [身体-右.stl, 身体-左.stl, 钩子.stl]
2023-04-09 [Fimeware]Add apriltag and sr handler
    [partitions.csv]
2023-04-12 [Fimeware]Update LED driver
2023-04-14 [Model]身体和手臂部分添加双电机方案
    [alram-r-t.stl, 身体-右.stl, 钩子.stl]
2023-04-15 [Model]添加双12g舵机方案，颈部零件合并至身体
    [alram-l-t.stl, alram-r-t.stl, 身体-右-12g舵机.stl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]
2023-04-16 [Model]Add alram-l/r-t-12g model
    [alram-l-t-12g.stl, alram-l-t-4.3g.stl, alram-r-t-12g.stl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]
2023-04-17 [Fimeware]Add vl53l0x device
2023-04-18 [Model]Update body and head model
    [身体-右-12g舵机.stl, 身体-头部-4.3g舵机.stl, 身体-左-12g舵机.stl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]
2023-04-23 [Model]Add 9g-servo-head/body model
    [身体-右-12g舵机.stl, 身体-右-9g舵机.stl, 身体-头部-12g舵机.stl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]
2023-05-07 [Model]Add sg90-body
    [身体-右-sg90.stl, 身体-头部--颈部.stl, 身体-头部-12g舵机.stl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]
2023-05-23 [Model]更新头部和身体模型
    [身体-右-sg90.stl, 身体-头部--颈部.stl, 身体-头部-无颈部.stl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]
2023-05-24 [Fimeware]更新lvgl版本-V8.3.7,添加GIF
2023-06-02 [model]修改身体模型
    [身体-头部--单独颈部.stl, 身体-头部.stl, 面部罩.stl]
2023-06-10 [Model]头部修改为两个模型，方便安装
    [头顶.stl, 身体-头部--右.stl, 身体-头部--左.stl]
2023-06-11 [Fimeware]更新查询vl53l0x为中断触发方式
2023-06-18 [Model]修改手部联接处为齿轮
    [alram-l-t-12g.stl, alram-l-t-bak.stl, alram-r-t-12g.stl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]
2023-06-19 [Model]优化部分模型，提升精度
    [alram-l-t-12g.stl, alram-r-t-12g.stl, 身体-头部--右.stl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]
2023-06-23 [fimeware]修改编译等级
2023-06-24 [Model]更新身体模型
2023-06-26 [Fimeware]更新舵机驱动
2023-07-02 [Model]更新4.3g舵机身体和手臂
    [alram-l-t-4.3g.stl, alram-r-t-4.3g.stl]
2023-07-09 [Model]更新身体和头部模型
    [身体-头部--左.stl, 面部罩.stl, 魔方主体.stl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]
2023-07-12 [Fimeware]添加pid相关驱动
2023-07-22 [fimeware]修改pid以及配置
2023-07-23 [fimerware]add position pid
2023-07-24 [fimeware]position pid
2023-07-25 [fimerware]add Incremental PID
2023-07-26 [fimeware]速度环添加低通滤波
2023-07-27 [Fimeware]add hardware i2c1
2023-07-28 [fimeware]更新i2c驱动
2023-07-30 [fimeware]Add angel pid
2023-08-05 [fimeware][head]adapter vscode plug
    [partitions.csv]
2023-08-05 [fimeware]修复头部固件，语音识别触发看门狗超时bug
2023-08-05 [fimeware][head]降低摄像头频率，使用jpeg方式读取
2023-08-06 [fimeware][head]修复摄像头JPEG初始化失败问题
2023-08-07 [fimeware][head]添加串口/舵机外设
2023-08-08 [fimeware][head]添加shell功能，格式化代码
2023-08-10 [fimeware][head]修改mp3播放结束自动暂停
2023-08-11 [hardware]更新Gerber
2023-08-15 [fimeware][head]添加emoji表情和唤醒逻辑
2023-08-18 [model]更新头部右侧模型
    [身体-头部--右.stl]
2023-08-19 [fimeware][head]播放器添加检索功能，裁剪表情尺寸
    [partitions.csv]
2023-08-19 [fimeware][head]添加openai组件，将ui和lcd分离
    [partitions.csv]
2023-08-22 [software]add unity proj
    [dumplicate.csv]
2023-08-23 [software]调整物体旋转中心与轴心重合
2023-08-24 [software]添加arm关节连接
2023-08-26 [software]添加滚动条
2023-08-27 [model]修改arm零件名称
    [alram-l-t.stl, alram-r-t.stl]
2023-08-27 [software]添加录制暂停按钮
2023-08-27 [software]添加串口部分
2023-08-28 [software]初步加入使用json保存动作数据
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2023-09-23 [model]更新魔方顶部模型
    [魔方顶部.stl]
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2023-10-18 [fimeware]删除servo-hal工程
    [configurations.h]
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2023-11-08 添加头部README
    [透明盖.step, 魔方主体.step, 魔方顶部.step]
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2023-11-13 修改音频文件，修复过爆问题
2023-11-17 [model]修改轮子模型名称
    [whell-smallx2.stl, whell1-bigx2.stl, whell2-bigx2.stl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]
2023-11-20 [model]扩大舵机插口
    [身体-头部--右.stl]
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2024-05-26 [model]修改头右部分模型
    [身体-头部--右.stl]
2024-07-06 [model]更新v1版本模型文件
    [alram-l-dx2.stl, alram-l-t-4.3g.stl, alram-l-t-bak.stl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]
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2024-07-28 [Fimeware]添加底盘bootloader源码
    [kconfig-language.txt, kconfig.txt]
2024-07-28 [rename]Rename Atom-Bot-Button to ATom-Bot-Chassis.
    [kconfig-language.txt, kconfig.txt]
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2024-08-03 [module]更新电池背仓模型，头部连接处加强筋
    [电池背仓.stl, 身体-头部--右.stl, 身体-头部--左.stl]
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2024-08-03 [model]删除不需要的模型
    [面部罩.stl]
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2024-08-11 [Chassis]修复中断上锁导致舵机控制实时性差的问题
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2024-09-16 [Chassis]修正轮子的位置环PID参数，简单实现跌落检测
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
